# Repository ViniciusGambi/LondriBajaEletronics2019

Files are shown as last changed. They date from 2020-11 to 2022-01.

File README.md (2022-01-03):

# LondriBajaEletronics2019

> Este repositório conta um pouco a jornada da evolução do subsistema de elétrica da equipe LondriBaja entre novembro de 2018 e março de 2020. Os detalhes de implementação de cada uma das partes do projeto citadas estão sendo adicionadas em repositórios individuais, as quais seus links são citados aqui ao longo desse texto.

## Jornada

Em Agosto de 2018, novatos na equipe, que naquele momento estava sem membros no subsistema de elétrica, topamos o desafio de mesmo sem estar cursando graduação nas áreas afins, estudar o necessário para conseguir levar um sistema de segurança robusto para a competição, que não gerasse alto número de rechecks para a equipe. A competição Regional Sul seria em outubro. Trabalhamos duro aqueles dois meses para isso. Conseguimos finalizar alguns dias antes da competição, e observando as necessidades da equipe para aquele momento, projetamos um simples sistema para aferir níveis baixos de combustível, de fabricação manual, bem simples, mas que funcionava. Conseguimos chegar na competição e o resultado foi 0 rechecks, e conseguimos uma boa nota, embora marinheiros de primeira viagem. O feedback dos juízes e experiências trocadas com as demais equipes nos mostravam que o segredo era começar com pouco, mas fazer bem feito. Isso nos deu ânimo e mostrava que estávamos no caminho certo. 

Iniciamos então uma nova fase. Definimos então algumas metas. O prazo final era a competição Nacional em março de 2020. Colheríamos mais feedbacks dos juízes nas competições Nacional de 2019, em fevereiro, e Regional Sul de novembro de 2020.

- Implementar o primeiro sistema de instrumentação desenvolvido pela equipe
- Otimizar a proteção contra líquidos do então atual sistema de segurança da equipe
- Desenvolver um sensor de baixo custo para aferir o deslocamento da suspensão
- Desenvolver um aplicativo que facilitasse o processo de fazer inspeções de segurança

### A instalação elétrica

Toda a instalação elétrica do veículo foi novamente projetada em busca de reduzir a massa total do sistema, torná-la mais robusta e mais resistente a líquidos, e mais modular em busca de acelerar o processo de manutenção. O chicote foi fabricado  com tubo anti chamas, conectores IP66, prensa-cabos.Foram projetadas caixas vedadas, fabricadas com impressão 3d e borrachas para a proteção contra líquidos dos botões de emergência.

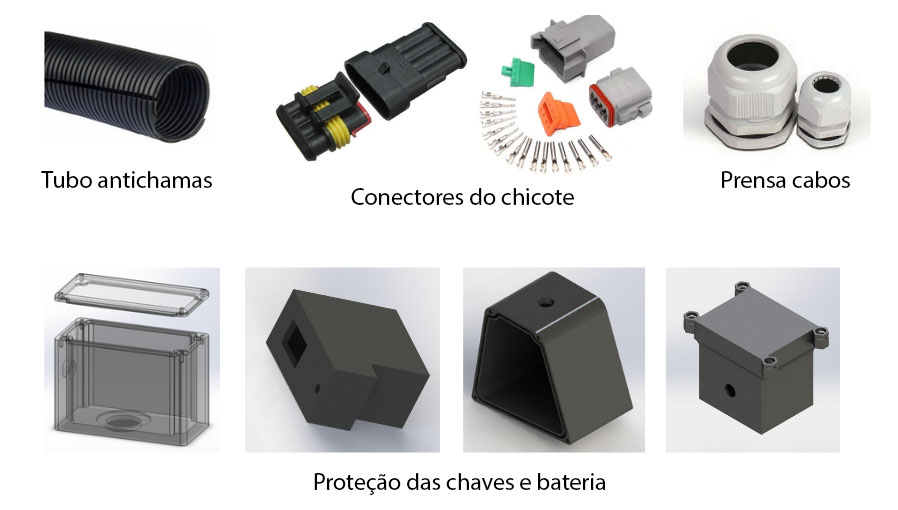
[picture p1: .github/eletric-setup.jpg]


### Sensoriamento

Seguindo o princípio de fazer algo enxuto, simples porém bem feito, para essa primeira versão foi optado por aferir 3 grandezas: RPM do motor, velocidade do veículo e nível de combustível. Os métodos escolhido para RPM foi extrair os pulsos gerados na bobina da vela, para a velocidade foi o posicionamento de um sensor indutivo no eixo da roda para contagem de pulsos, e para o combustível posicionar sensores capacitivos digitais externos ao tanque (visto que a competição proíbe utilizar sensores dentro do tanque). Mais detalhes podem ser vistos nos repositórios individuais (a serem criados).

### Projeto Elétrico e Eletrônico

O diagrama abaixo mostra como ficou organizado o sistema de segurança junto ao sistema eletrônico. 

O sistema eletrônico foi dividido em duas PCB’s, uma ECU, principal, que cuida do do controle das tensões, conecta o microcontrolador, que trabalha os dados, as entradas dos sensores, e expõe os dados para a Serial e outra PCB, que é um display com leds e displays de 7 segmentos que é utilizada como painel. 
O controle das tensões é feito por dois reguladores buck por apresentarem eficiências mais altas. O microcontrolador, um ATMega328p, foi escolhido para garantir o andamento do projeto no futuro da equipe. Como em nossa universidade não temos alunos cursando a área de eletrônica e afins, essa escolha facilita para que o projeto não fique estagnado até que futuros novos membros possam aprender a programar microcontroladores de baixo nível, pelo fato desse microcontrolador poder ser programado com a biblioteca Arduino, que tem uma grande comunidade e é de fácil aprendizagem. E mesmo assim, se adequa aos requisitos do projeto, atendendo as necessidades do projeto. Os esquemáticos e detalhes da implementação podem ser extraídos nos repositório X.

Foram projetadas caixas vedadas, como as do sistema de segurança, para o sistema de instrumentação. Foram desenvolvidas duas versões das caixas de proteção nesse tempo. A primeira foi projetada em forma de gaveta, em busca de fácil manutenção caso necessário, e guardava ambas as duas PCBs. É a implementada no veículo ao fim deste projeto. A segunda versão separa as PCB’s em duas caixas, em busca de maior modularidade, e substitui os conectores que são utilizadas na primeira versão, por sensores automotivos que se conectam diretamente a PCB, para tornar a solução mais automotiva, e retirar os prensa-cabos. Essa versão será fabricada em 2020, mas o projeto já está pronto ao fim deste ciclo. 

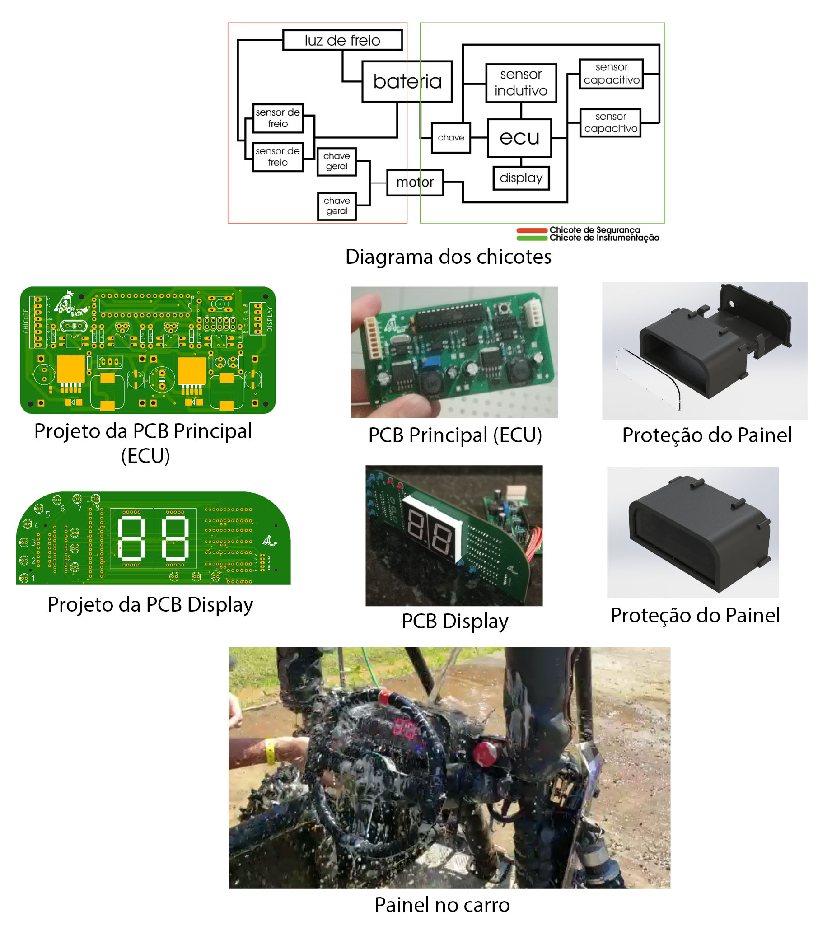
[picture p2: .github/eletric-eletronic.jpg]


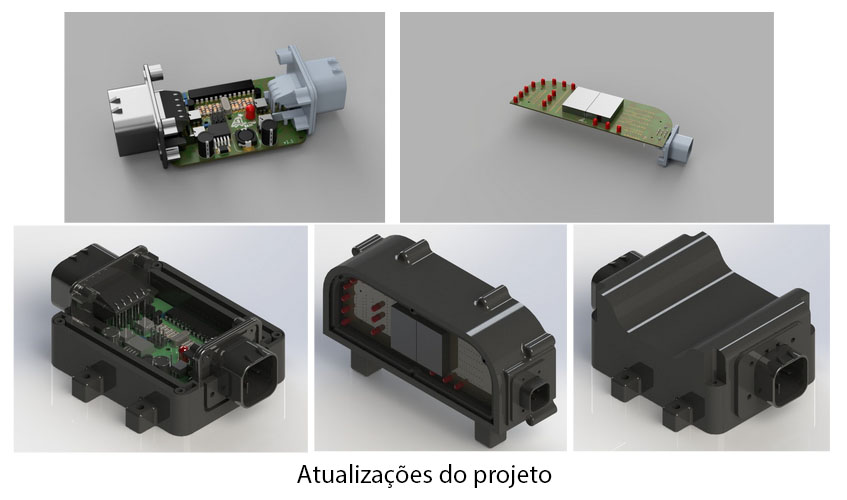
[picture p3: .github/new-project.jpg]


### User Interface e Registro de dados

Para exibir os dados aferidos pelo sistema de instrumentação, foi desenhada uma interface para a exibição dos dados. Para o registro de dados para análises, foi desenvolvido um aplicativo Android que faz registro (como um data logger) dos dados expostos na Serial. (link aqui)

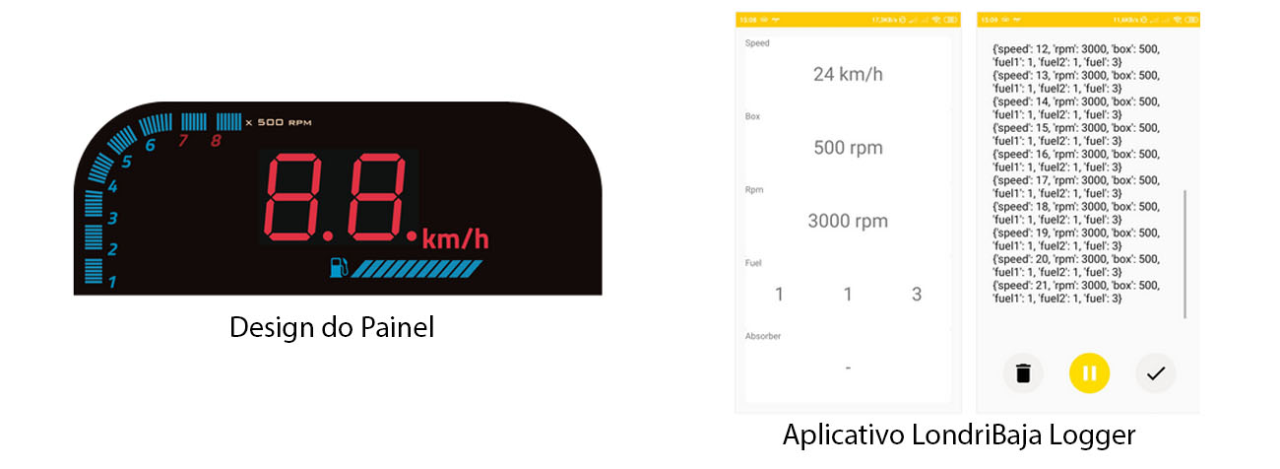
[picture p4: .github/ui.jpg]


### Validação

Todas as grandezas aferidas foram validadas e ajustadas com equipamentos com valores de referência confiáveis. A validação de RPM do motor foi feita por meio de um tacômetro óptico em bancada. Os valores de combustível foram validados em laboratório. Para a velocidade, pela falta de acesso a um equipamento calibrado de referência, desenvolvemos uma aplicação que extrai os dados de velocidade do aplicativo Waze (por ser a fonte mais segura acessível a equipe) por processamento de imagem, e os guarda registrados em função do tempo em uma planilha para a análise e comparação posterior.

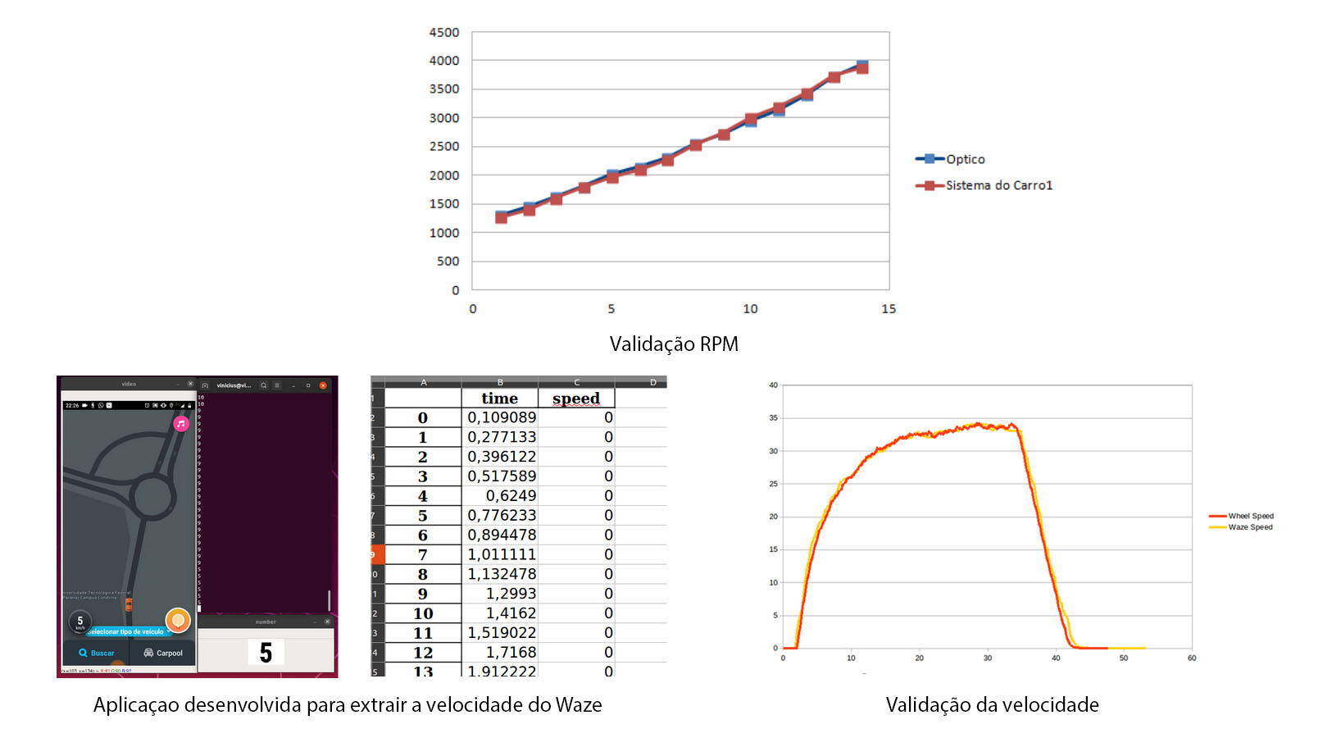
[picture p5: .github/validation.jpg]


### Extra

A partir de uma necessidade do subsistema de suspensão, que precisava de dados de deslocamento da suspensão, verificamos a possibilidade da compra de um sensor para isso. Como o valor escapava ao orçamento, buscamos uma forma de aferir essa grandeza com um sensor de baixo custo. Inicialmente realizamos alguns testes com um acelerômetro MPU6050, entretanto em virtude da baixa precisão do sensor, o acúmulo de erros ao longo do tempo tornava inviável a integral da aceleração para retirar o deslocamento. Desenvolvemos então uma solução melhor, barata, mais robusta, e com grande precisão com impressão 3D, duas barras lineares e um encoder óptico aproveitados de uma impressora velha. Esse projeto pode ser visualizado nesse outro repositório (a ser upado). 

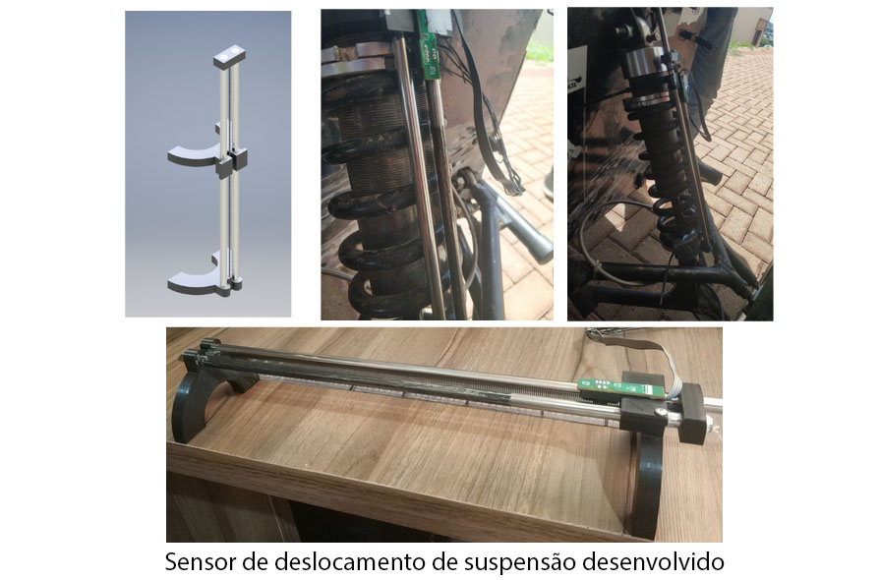
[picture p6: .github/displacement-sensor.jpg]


Outro projeto desenvolvido no ano foi um aplicativo para tornar fácil e rápido o processo da inspeção de segurança, possibilitando que a equipe os faça com mais frequência, com o objetivo de ajudar na redução dos rechecks da equipe. O link do repositório desse projeto será adicionado aqui.

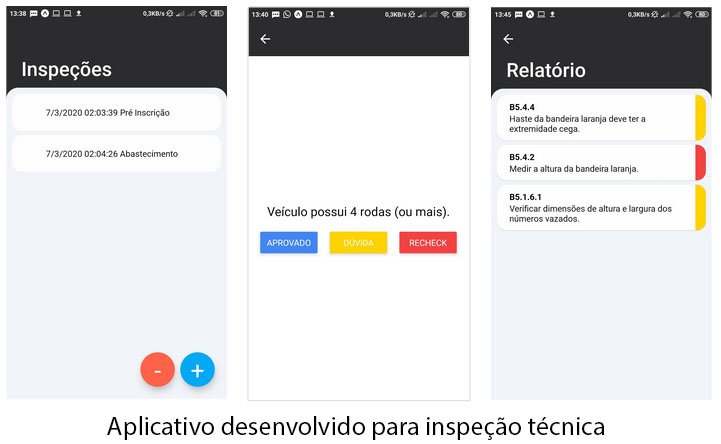
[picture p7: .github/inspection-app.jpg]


### Resultados

Com as implementações feitas, os objetivos citados anteriormente foram atingidos. Ficamos contentes por nossa evolução nesse período. Saímos de uma equipe que não tinha notas de projeto elétrico até então para o 3º melhor projeto eletrônico do Regional Sul 2019 (entre as 31 equipes inscritas) e o 13º (entre as 78 inscritas) no Nacional 2020. Deixaremos aqui também o banner da apresentação final desse projeto no Nacional de Março de 2020.

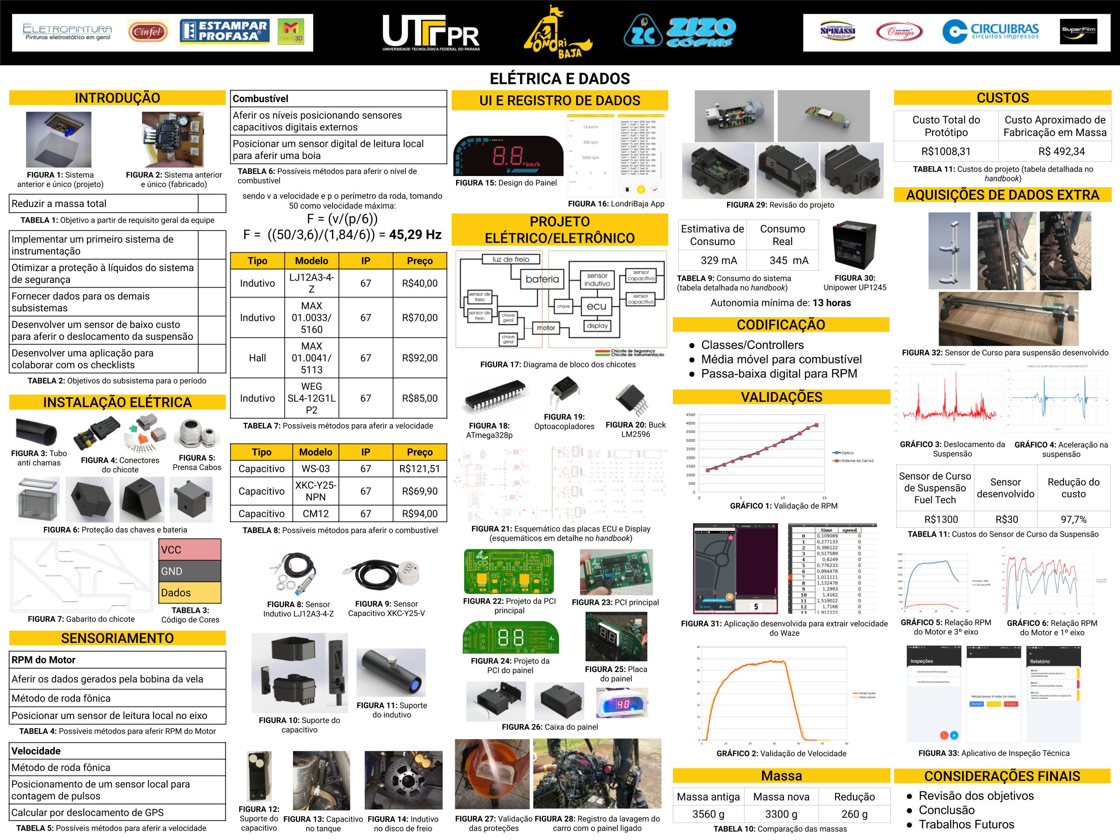
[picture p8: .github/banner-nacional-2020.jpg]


## Os autores

Cauê Gaffo, Giovani David e Vinicius Gambi abraçaram o subsistema e lideraram esse processo. No meio de 2019, tivemos a chegada dos trainees Ana Gama, Beatriz Yukari e Victor Toshio que muito ajudaram na fabricação e manutenção do projeto, e darão os próximos passos nessa evolução.

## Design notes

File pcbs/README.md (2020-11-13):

### v1

<p align="center">
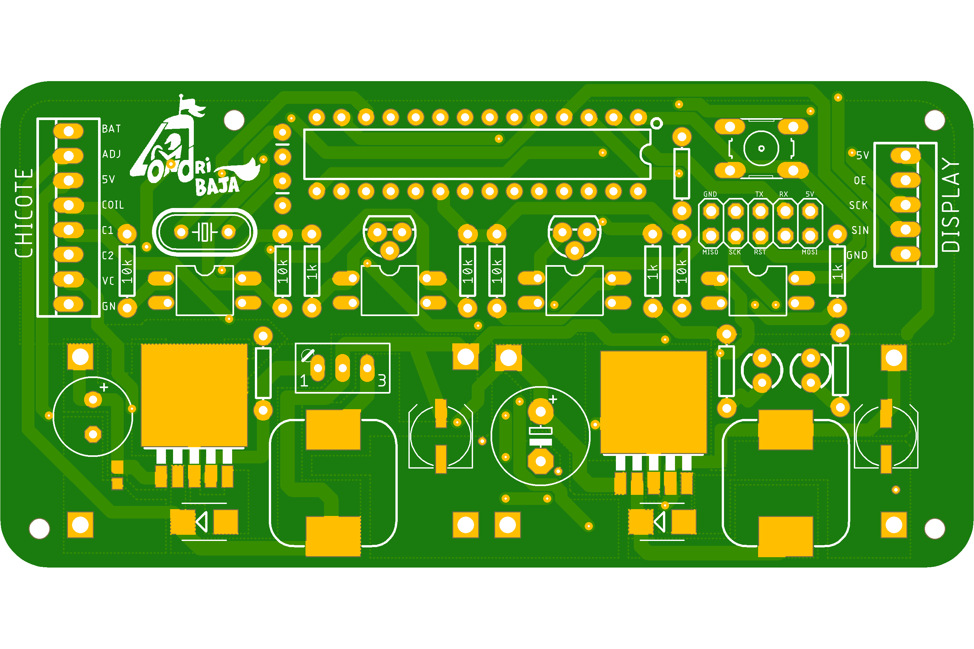
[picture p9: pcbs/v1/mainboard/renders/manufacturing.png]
    
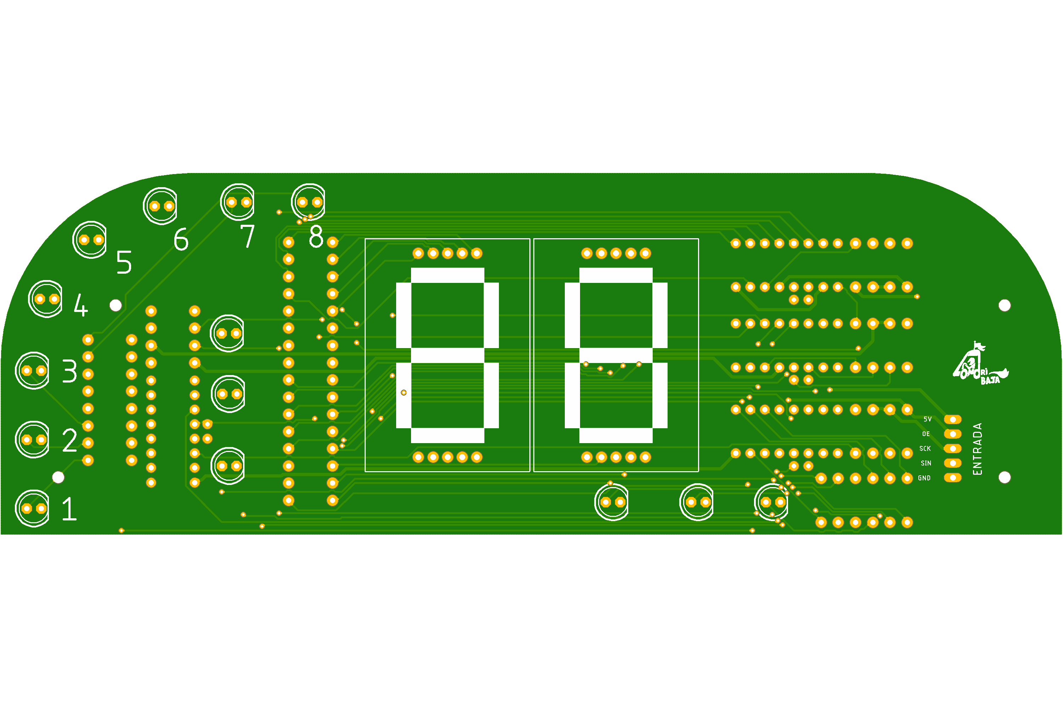
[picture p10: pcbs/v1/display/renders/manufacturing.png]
    
</p>

### v2

<p align="center">
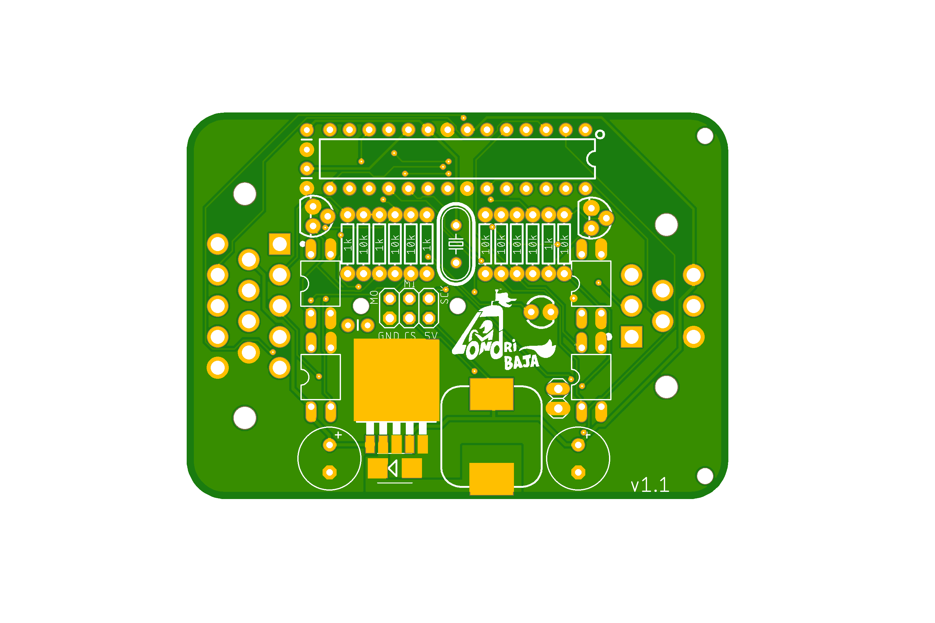
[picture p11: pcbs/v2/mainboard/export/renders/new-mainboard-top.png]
    
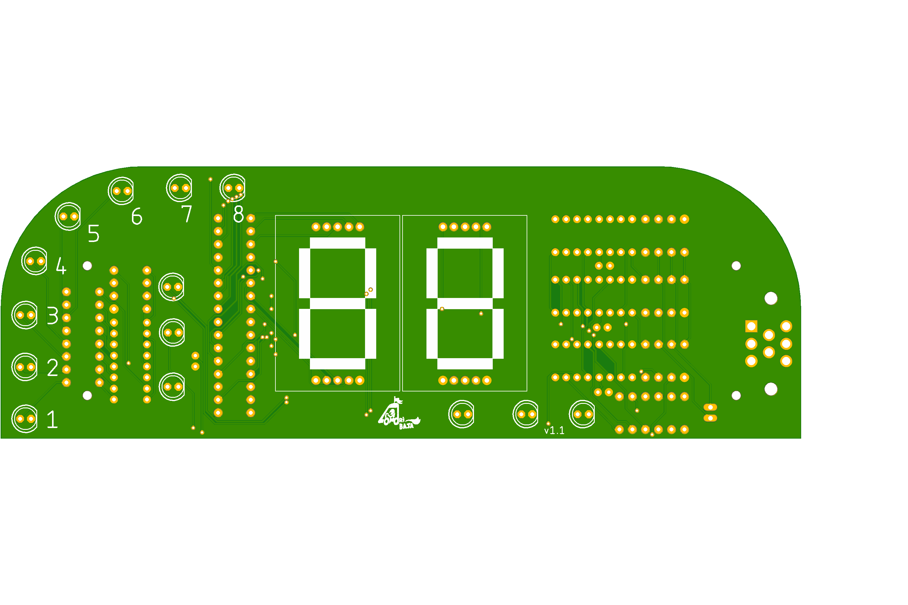
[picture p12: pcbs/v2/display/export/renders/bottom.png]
    
</p>

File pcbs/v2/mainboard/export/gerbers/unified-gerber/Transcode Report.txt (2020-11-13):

   ---- Transcoding 'C:\Users\Workstation\Documents\Baja 2020\pcbs\out\unified-gerber\combined.gbs' ----   Wed Feb 19 16:48:30 2020

D10   --> D100
D11   --> D101
D12   --> D102
D13   --> D103
D14   --> D104
D15   --> D105
D16   --> D106
D17   --> D107
D18   --> D108
D19   --> D109
D20   --> D110
D21   --> D111
D22   --> D112
D23   --> D113
D24   --> D114
D36   --> D115
D37   --> D116
D38   --> D117
D39   --> D118
D40   --> D119
D41   --> D120
D42   --> D121
D43   --> D122
D44   --> D123
-----------------------------------------------------------------

   ---- Transcoding 'C:\Users\Workstation\Documents\Baja 2020\pcbs\out\unified-gerber\combined.GKO' ----   Wed Feb 19 16:48:30 2020

D10   --> D124
-----------------------------------------------------------------

   ---- Transcoding 'C:\Users\Workstation\Documents\Baja 2020\pcbs\out\unified-gerber\combined.gml' ----   Wed Feb 19 16:48:30 2020

D10   --> D125
D11   --> D126
D22   --> D127
D23   --> D128
-----------------------------------------------------------------

   ---- Transcoding 'C:\Users\Workstation\Documents\Baja 2020\pcbs\out\unified-gerber\combined.gtl' ----   Wed Feb 19 16:48:30 2020

D15   --> D129
D16   --> D130
D17   --> D131
D18   --> D132
D19   --> D133
D20   --> D134
D21   --> D135
D22   --> D136
D23   --> D137
D24   --> D138
D25   --> D139
D42   --> D140
D43   --> D141
D44   --> D142
-----------------------------------------------------------------

   ---- Transcoding 'C:\Users\Workstation\Documents\Baja 2020\pcbs\out\unified-gerber\combined.gtp' ----   Wed Feb 19 16:48:32 2020

D10   --> D143
D11   --> D144
D12   --> D145
D13   --> D146
-----------------------------------------------------------------

   ---- Transcoding 'C:\Users\Workstation\Documents\Baja 2020\pcbs\out\unified-gerber\combined.gts' ----   Wed Feb 19 16:48:32 2020

D10   --> D147
D11   --> D148
D12   --> D149
D13   --> D150
D14   --> D151
D15   --> D152
D16   --> D153
D17   --> D154
D18   --> D155
D19   --> D156
D20   --> D157
D21   --> D158
D22   --> D159
D23   --> D160
D24   --> D161
D25   --> D162
D26   --> D163
D27   --> D164
D28   --> D165
D39   --> D166
D40   --> D167
D41   --> D168
D42   --> D169
D43   --> D170
D44   --> D171
D45   --> D172
D46   --> D173
D47   --> D174
D48   --> D175
-----------------------------------------------------------------

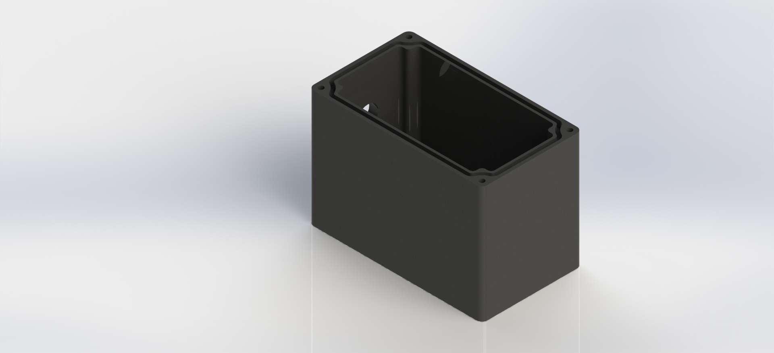
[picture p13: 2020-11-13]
mechanical/v2/renders/caixa-botao-piloto.JPG

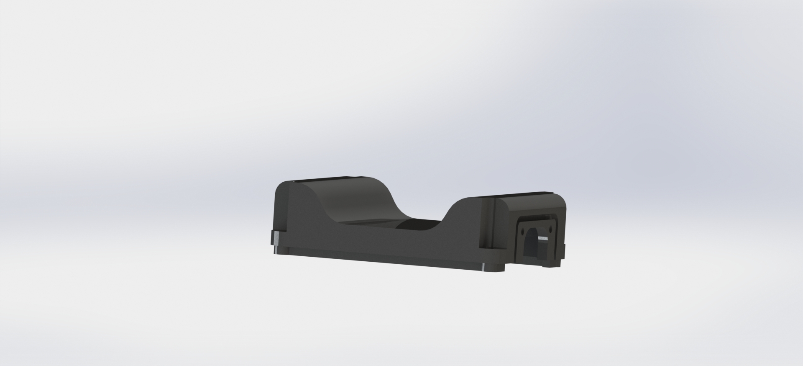
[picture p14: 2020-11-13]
mechanical/v2/renders/tampa-mainboard-3.JPG

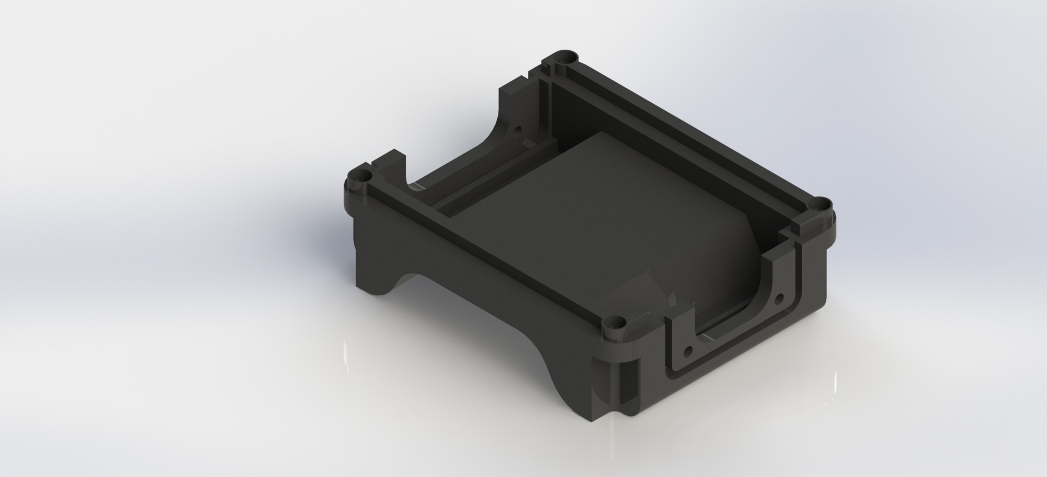
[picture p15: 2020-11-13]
mechanical/v2/renders/tampa-mainboard-1.JPG

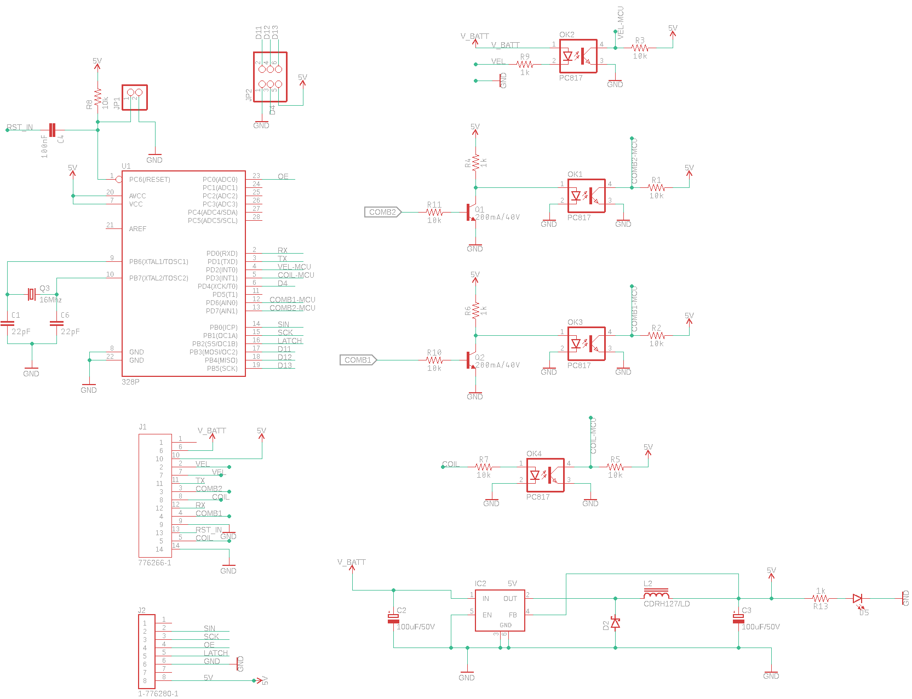
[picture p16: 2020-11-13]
pcbs/v2/mainboard/export/renders/schematic.png

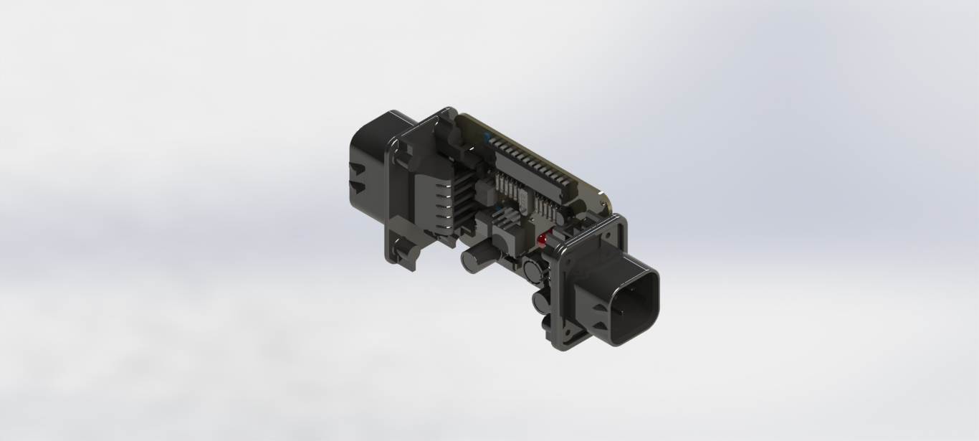
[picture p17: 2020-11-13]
mechanical/v2/renders/mainboard.JPG

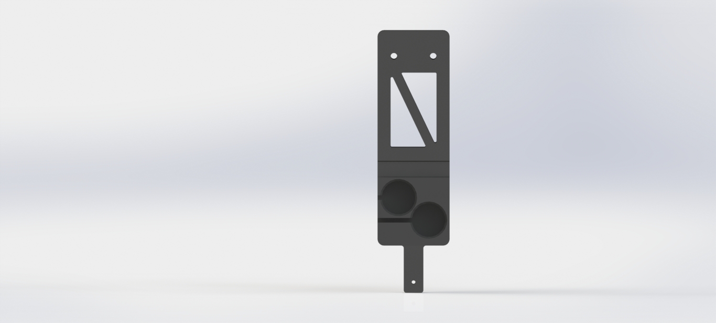
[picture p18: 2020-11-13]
mechanical/v2/renders/suporte-sensor-combustivel-2.JPG

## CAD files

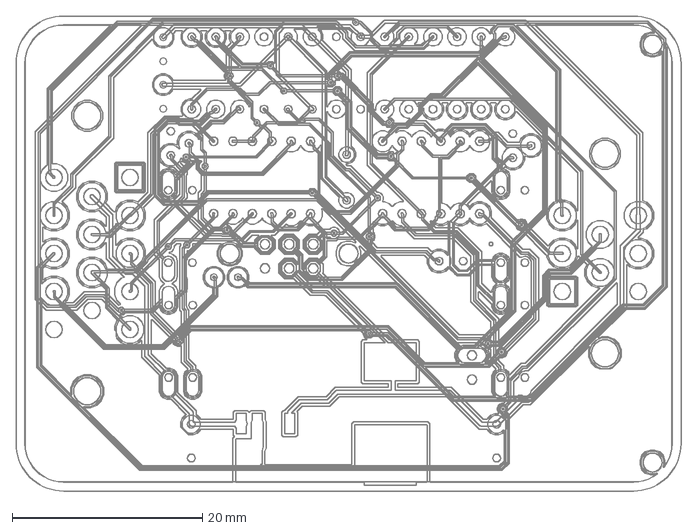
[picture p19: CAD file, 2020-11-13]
pcbs/v2/mainboard/export/dxf/new-mainboard.dxf
70.0 x 50.0 mm

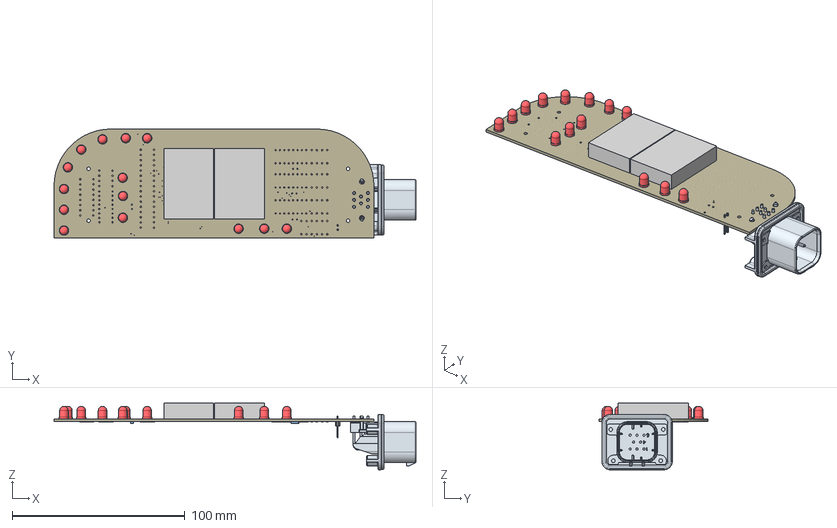
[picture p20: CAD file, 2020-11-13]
pcbs/v2/display/export/step/new-display.step
209.3 x 63.0 x 38.6 mm
Board
LED5MM x 14
DISPLAY1.2 x 2
SN74HC595N x 4
0.1uF x 4
1X02

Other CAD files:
pcbs/v2/display/export/dxf/new-display.dxf

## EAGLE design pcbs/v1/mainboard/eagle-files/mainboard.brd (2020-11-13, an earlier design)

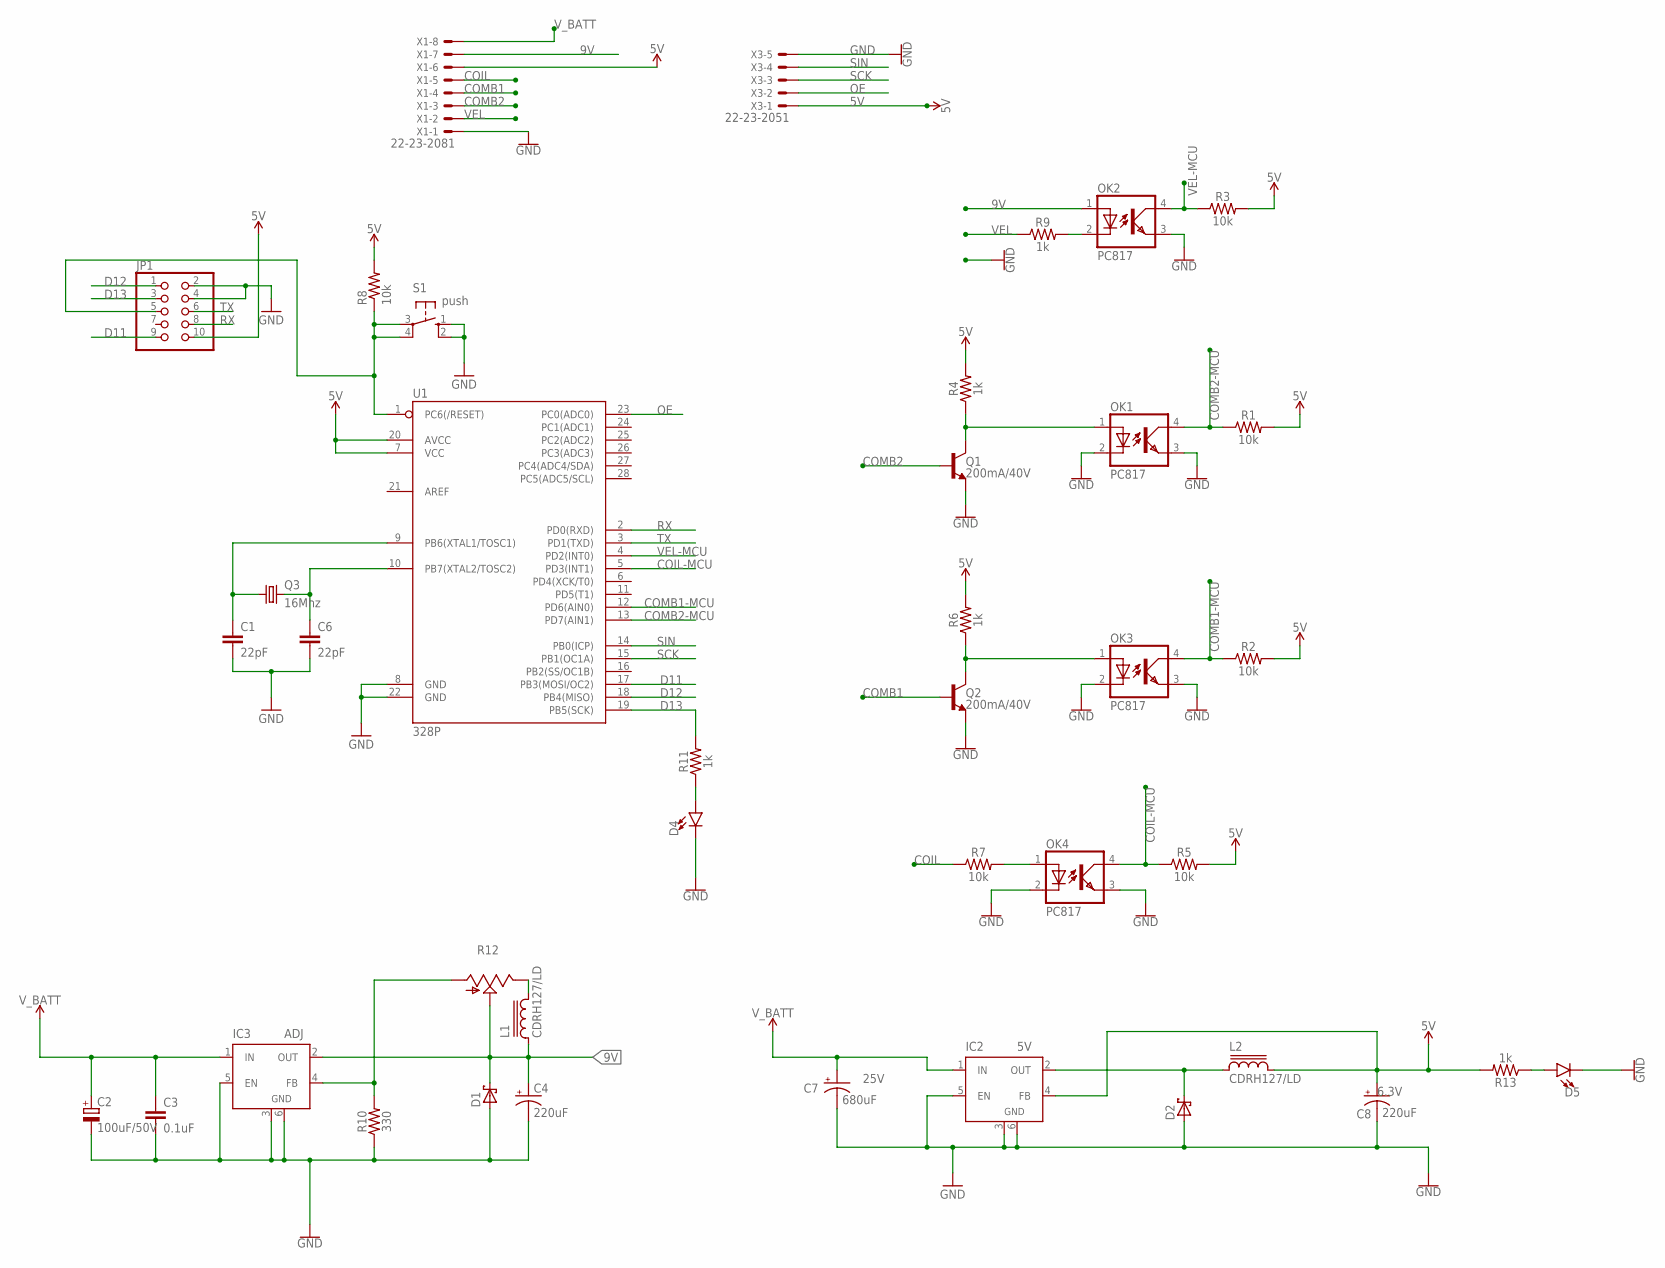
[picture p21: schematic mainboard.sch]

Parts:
C1, C6: 22pF; CAP-PTH-2.54
C2: 100uF/50V; E3,5-8
C3: 0.1uF; 0603
C4: 220uF; UD-6,3X5,8_NICHICON
C7: 680uF; E5-10,5; VOLTAGE 25V
C8: 220uF; UD-6,3X5,8_NICHICON; VOLTAGE 6.3V
D1, D2: SCHOTTKY-DIODESMD; SMB
D4, D5: LED3MM; LED_3MM
IC2: 5V; TO263-5
IC3: ADJ; TO263-5
JP1: PINHD-2X5; 2X05
L1, L2: CDRH127/LD
OK1, OK2, OK3, OK4: PC817; DIL04
Q1, Q2: 200mA/40V; TO-92
Q3: 16Mhz; HC49U-V
R1, R2, R3, R5, R7, R8: 10k; AXIAL-0.3
R4, R6, R9, R11, R13: 1k; AXIAL-0.3
R10: 330; AXIAL-0.3
R12: TRIM_US-S64W; S64W
S1: push; B3F-10XX
U1: 328P; DIP28
X1: 22-23-2081
X3: 22-23-2051

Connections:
5V: C8.+, IC2.4 (FB), JP1.10, L2.2, R1.P$2 (2), R2.P$2 (2), R3.P$2 (2), R4.P$2 (2), R5.P$2 (2), R6.P$2 (2), R8.P$2 (2), R13.P$2 (2), U1.7 (VCC), U1.20 (AVCC), X1.6, X3.1
9V: C4.+, D1.C, IC3.2 (OUT), L1.1, OK2.1 (A), R12.S, X1.7
COIL: R7.P$1 (1), X1.5
COIL-MCU: OK4.4 (COL), R5.P$1 (1), U1.5 (PD3(INT1))
COMB1: Q2.2 (B), X1.4
COMB1-MCU: OK3.4 (COL), R2.P$1 (1), U1.12 (PD6(AIN0))
COMB2: Q1.2 (B), X1.3
COMB2-MCU: OK1.4 (COL), R1.P$1 (1), U1.13 (PD7(AIN1))
D11: JP1.9, U1.17 (PB3(MOSI/OC2))
D12: JP1.1, U1.18 (PB4(MISO))
D13: JP1.3, R11.P$2 (2), U1.19 (PB5(SCK))
GND: C1.2, C2.-, C3.2, C4.-, C6.2, C7.-, C8.-, D1.A, D2.A, D4.K (C), D5.K (C), IC2.3 (GND), IC2.5 (EN), IC2.6 (GND), IC3.3 (GND), IC3.5 (EN), IC3.6 (GND), JP1.2, JP1.4, OK1.2 (C), OK1.3 (EMIT), OK2.3 (EMIT), OK3.2 (C), OK3.3 (EMIT), OK4.2 (C), OK4.3 (EMIT), Q1.1 (E), Q2.1 (E), R10.P$1 (1), S1.1 (S), S1.2 (S1), U1.8 (GND), U1.22 (GND), X1.1, X3.5
unnamed: OK4.1 (A), R7.P$2 (2)
unnamed: OK2.2 (C), R9.P$2 (2)
unnamed: OK1.1 (A), Q1.3 (C), R4.P$1 (1)
unnamed: OK3.1 (A), Q2.3 (C), R6.P$1 (1)
unnamed: C1.1, Q3.1, U1.9 (PB6(XTAL1/TOSC1))
unnamed: C6.1, Q3.2, U1.10 (PB7(XTAL2/TOSC2))
unnamed: JP1.5, R8.P$1 (1), S1.3, S1.4 (P1), U1.1 (PC6(/RESET))
unnamed: D5.A, R13.P$1 (1)
unnamed: L1.2, R12.E
unnamed: IC3.4 (FB), R10.P$2 (2), R12.A
unnamed: D4.A, R11.P$1 (1)
OE: U1.23 (PC0(ADC0)), X3.2
OUT: D2.C, IC2.2 (OUT), L2.1
RX: JP1.8, U1.2 (PD0(RXD))
SCK: U1.15 (PB1(OC1A)), X3.3
SIN: U1.14 (PB0(ICP)), X3.4
TX: JP1.6, U1.3 (PD1(TXD))
VEL: R9.P$1 (1), X1.2
VEL-MCU: OK2.4 (COL), R3.P$1 (1), U1.4 (PD2(INT0))
V_BATT: C2.+, C3.1, C7.+, IC2.1 (IN), IC3.1 (IN), X1.8

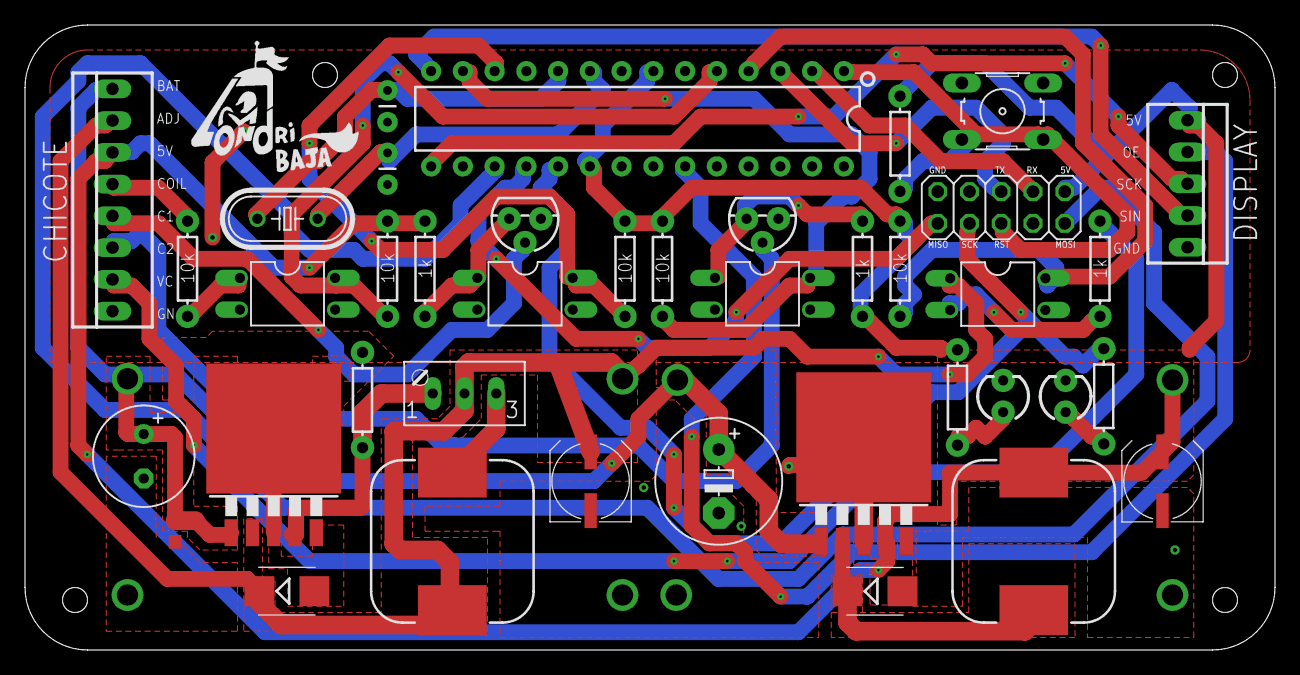
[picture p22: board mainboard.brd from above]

Board: 2 copper layers, 100.0 x 50.0 mm, 40 parts (0 on the bottom side), 32 nets.

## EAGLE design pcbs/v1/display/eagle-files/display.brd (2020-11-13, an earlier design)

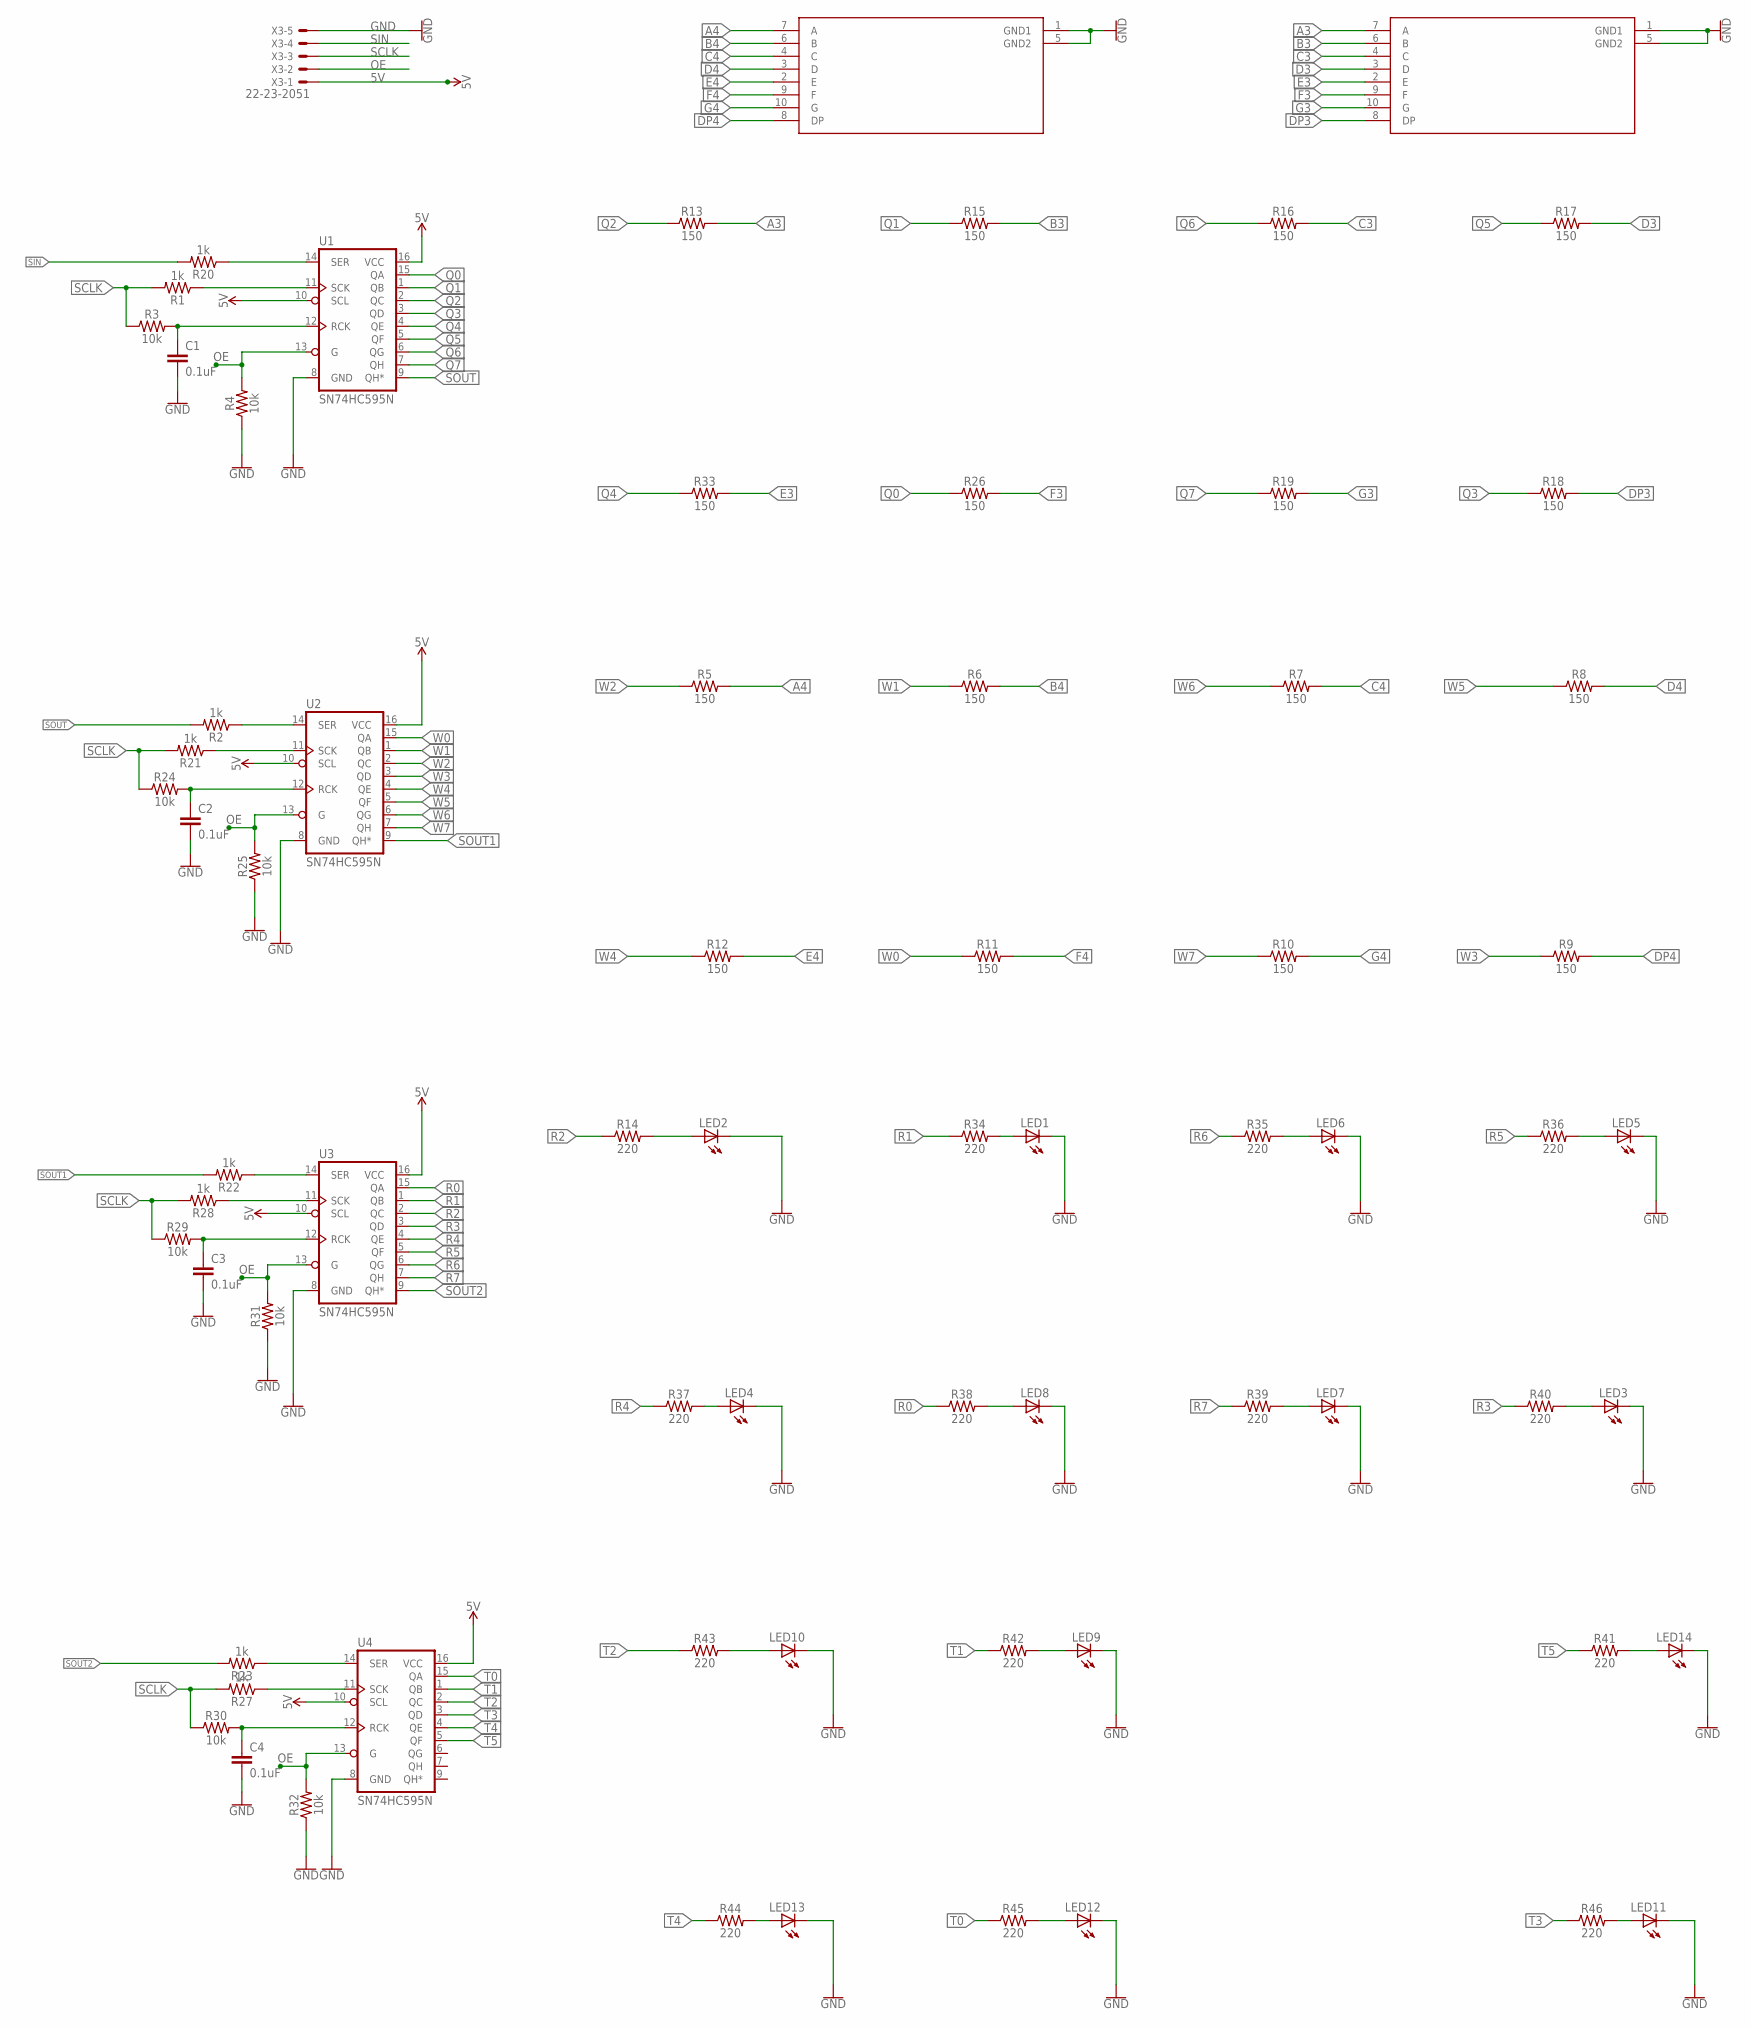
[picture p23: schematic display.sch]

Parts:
C1, C2, C3, C4: 0.1uF; CAP-PTH-2.54
LED1, LED2, LED3, LED4, LED5, LED6, LED7, LED8, LED9, LED10, LED11, LED12, LED13, LED14: LED5MM
R1, R2, R20, R21, R22, R23, R27, R28: 1k; AXIAL-0.3
R3, R4, R24, R25, R29, R30, R31, R32: 10k; AXIAL-0.3
R5, R6, R7, R8, R9, R10, R11, R12, R13, R15, R16, R17, R18, R19, R26, R33: 150; AXIAL-0.3
R14, R34, R35, R36, R37, R38, R39, R40, R41, R42, R43, R44, R45, R46: 220; AXIAL-0.3
U1, U2, U3, U4: SN74HC595N; DIP16
U$1, U$2: DISPLAY1.2; 1.2INCH
X3: 22-23-2051

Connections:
5V: U1.10 (SCL), U1.16 (VCC), U2.10 (SCL), U2.16 (VCC), U3.10 (SCL), U3.16 (VCC), U4.10 (SCL), U4.16 (VCC), X3.1
A3: R13.P$2 (2), U$1.7 (A)
A4: R5.P$2 (2), U$2.7 (A)
B3: R15.P$2 (2), U$1.6 (B)
B4: R6.P$2 (2), U$2.6 (B)
C3: R16.P$2 (2), U$1.4 (C)
C4: R7.P$2 (2), U$2.4 (C)
D3: R17.P$2 (2), U$1.3 (D)
D4: R8.P$2 (2), U$2.3 (D)
DP3: R18.P$2 (2), U$1.8 (DP)
DP4: R9.P$2 (2), U$2.8 (DP)
E3: R33.P$2 (2), U$1.2 (E)
E4: R12.P$2 (2), U$2.2 (E)
F3: R26.P$2 (2), U$1.9 (F)
F4: R11.P$2 (2), U$2.9 (F)
G3: R19.P$2 (2), U$1.10 (G)
G4: R10.P$2 (2), U$2.10 (G)
GND: C1.2, C2.2, C3.2, C4.2, LED1.K (C), LED2.K (C), LED3.K (C), LED4.K (C), LED5.K (C), LED6.K (C), LED7.K (C), LED8.K (C), LED9.K (C), LED10.K (C), LED11.K (C), LED12.K (C), LED13.K (C), LED14.K (C), R4.P$1 (1), R25.P$1 (1), R31.P$1 (1), R32.P$1 (1), U1.8 (GND), U2.8 (GND), U3.8 (GND), U4.8 (GND), U$1.1 (GND1), U$1.5 (GND2), U$2.1 (GND1), U$2.5 (GND2), X3.5
unnamed: R20.P$1 (1), U1.14 (SER)
unnamed: R1.P$1 (1), U1.11 (SCK)
unnamed: C1.1, R3.P$2 (2), U1.12 (RCK)
unnamed: R2.P$1 (1), U2.14 (SER)
unnamed: R21.P$1 (1), U2.11 (SCK)
unnamed: C2.1, R24.P$2 (2), U2.12 (RCK)
unnamed: LED4.A, R37.P$2 (2)
unnamed: LED8.A, R38.P$2 (2)
unnamed: LED7.A, R39.P$2 (2)
unnamed: LED3.A, R40.P$2 (2)
unnamed: LED5.A, R36.P$2 (2)
unnamed: LED6.A, R35.P$2 (2)
unnamed: LED1.A, R34.P$2 (2)
unnamed: LED2.A, R14.P$2 (2)
unnamed: LED10.A, R43.P$2 (2)
unnamed: R22.P$1 (1), U3.14 (SER)
unnamed: R28.P$1 (1), U3.11 (SCK)
unnamed: C3.1, R29.P$2 (2), U3.12 (RCK)
unnamed: LED9.A, R42.P$2 (2)
unnamed: LED11.A, R46.P$2 (2)
unnamed: LED14.A, R41.P$2 (2)
unnamed: LED12.A, R45.P$2 (2)
unnamed: R23.P$1 (1), U4.14 (SER)
unnamed: R27.P$1 (1), U4.11 (SCK)
unnamed: C4.1, R30.P$2 (2), U4.12 (RCK)
unnamed: LED13.A, R44.P$2 (2)
OE: R4.P$2 (2), R25.P$2 (2), R31.P$2 (2), R32.P$2 (2), U1.13 (G), U2.13 (G), U3.13 (G), U4.13 (G), X3.2
Q0: R26.P$1 (1), U1.15 (QA)
Q1: R15.P$1 (1), U1.1 (QB)
Q2: R13.P$1 (1), U1.2 (QC)
Q3: R18.P$1 (1), U1.3 (QD)
Q4: R33.P$1 (1), U1.4 (QE)
Q5: R17.P$1 (1), U1.5 (QF)
Q6: R16.P$1 (1), U1.6 (QG)
Q7: R19.P$1 (1), U1.7 (QH)
R0: R38.P$1 (1), U3.15 (QA)
R1: R34.P$1 (1), U3.1 (QB)
R2: R14.P$1 (1), U3.2 (QC)
R3: R40.P$1 (1), U3.3 (QD)
R4: R37.P$1 (1), U3.4 (QE)
R5: R36.P$1 (1), U3.5 (QF)
R6: R35.P$1 (1), U3.6 (QG)
R7: R39.P$1 (1), U3.7 (QH)
SCLK: R1.P$2 (2), R3.P$1 (1), R21.P$2 (2), R24.P$1 (1), R27.P$2 (2), R28.P$2 (2), R29.P$1 (1), R30.P$1 (1), X3.3
SIN: R20.P$2 (2), X3.4
SOUT: R2.P$2 (2), U1.9 (QH*)
SOUT1: R22.P$2 (2), U2.9 (QH*)
SOUT2: R23.P$2 (2), U3.9 (QH*)
T0: R45.P$1 (1), U4.15 (QA)
T1: R42.P$1 (1), U4.1 (QB)
T2: R43.P$1 (1), U4.2 (QC)
T3: R46.P$1 (1), U4.3 (QD)
T4: R44.P$1 (1), U4.4 (QE)
T5: R41.P$1 (1), U4.5 (QF)
W0: R11.P$1 (1), U2.15 (QA)
W1: R6.P$1 (1), U2.1 (QB)
W2: R5.P$1 (1), U2.2 (QC)
W3: R9.P$1 (1), U2.3 (QD)
W4: R12.P$1 (1), U2.4 (QE)
W5: R8.P$1 (1), U2.5 (QF)
W6: R7.P$1 (1), U2.6 (QG)
W7: R10.P$1 (1), U2.7 (QH)

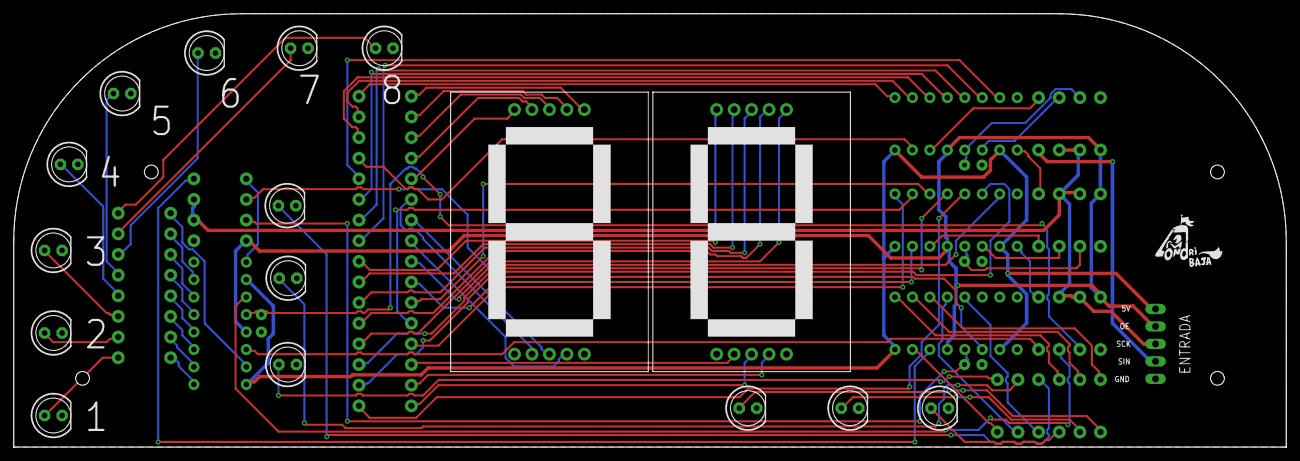
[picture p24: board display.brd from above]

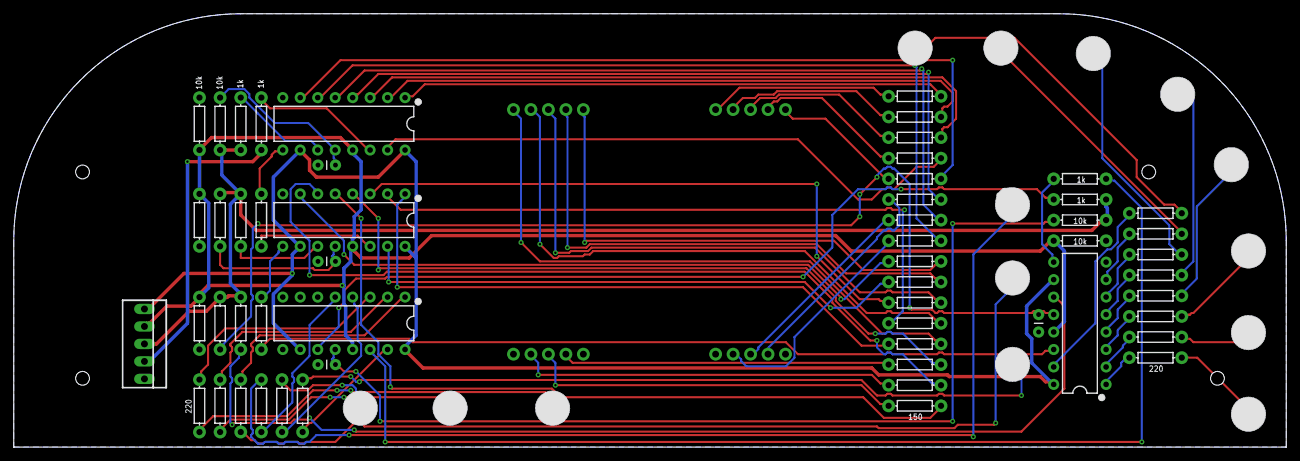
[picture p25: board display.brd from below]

Board: 2 copper layers, 185.0 x 63.0 mm, 71 parts (55 on the bottom side), 80 nets.

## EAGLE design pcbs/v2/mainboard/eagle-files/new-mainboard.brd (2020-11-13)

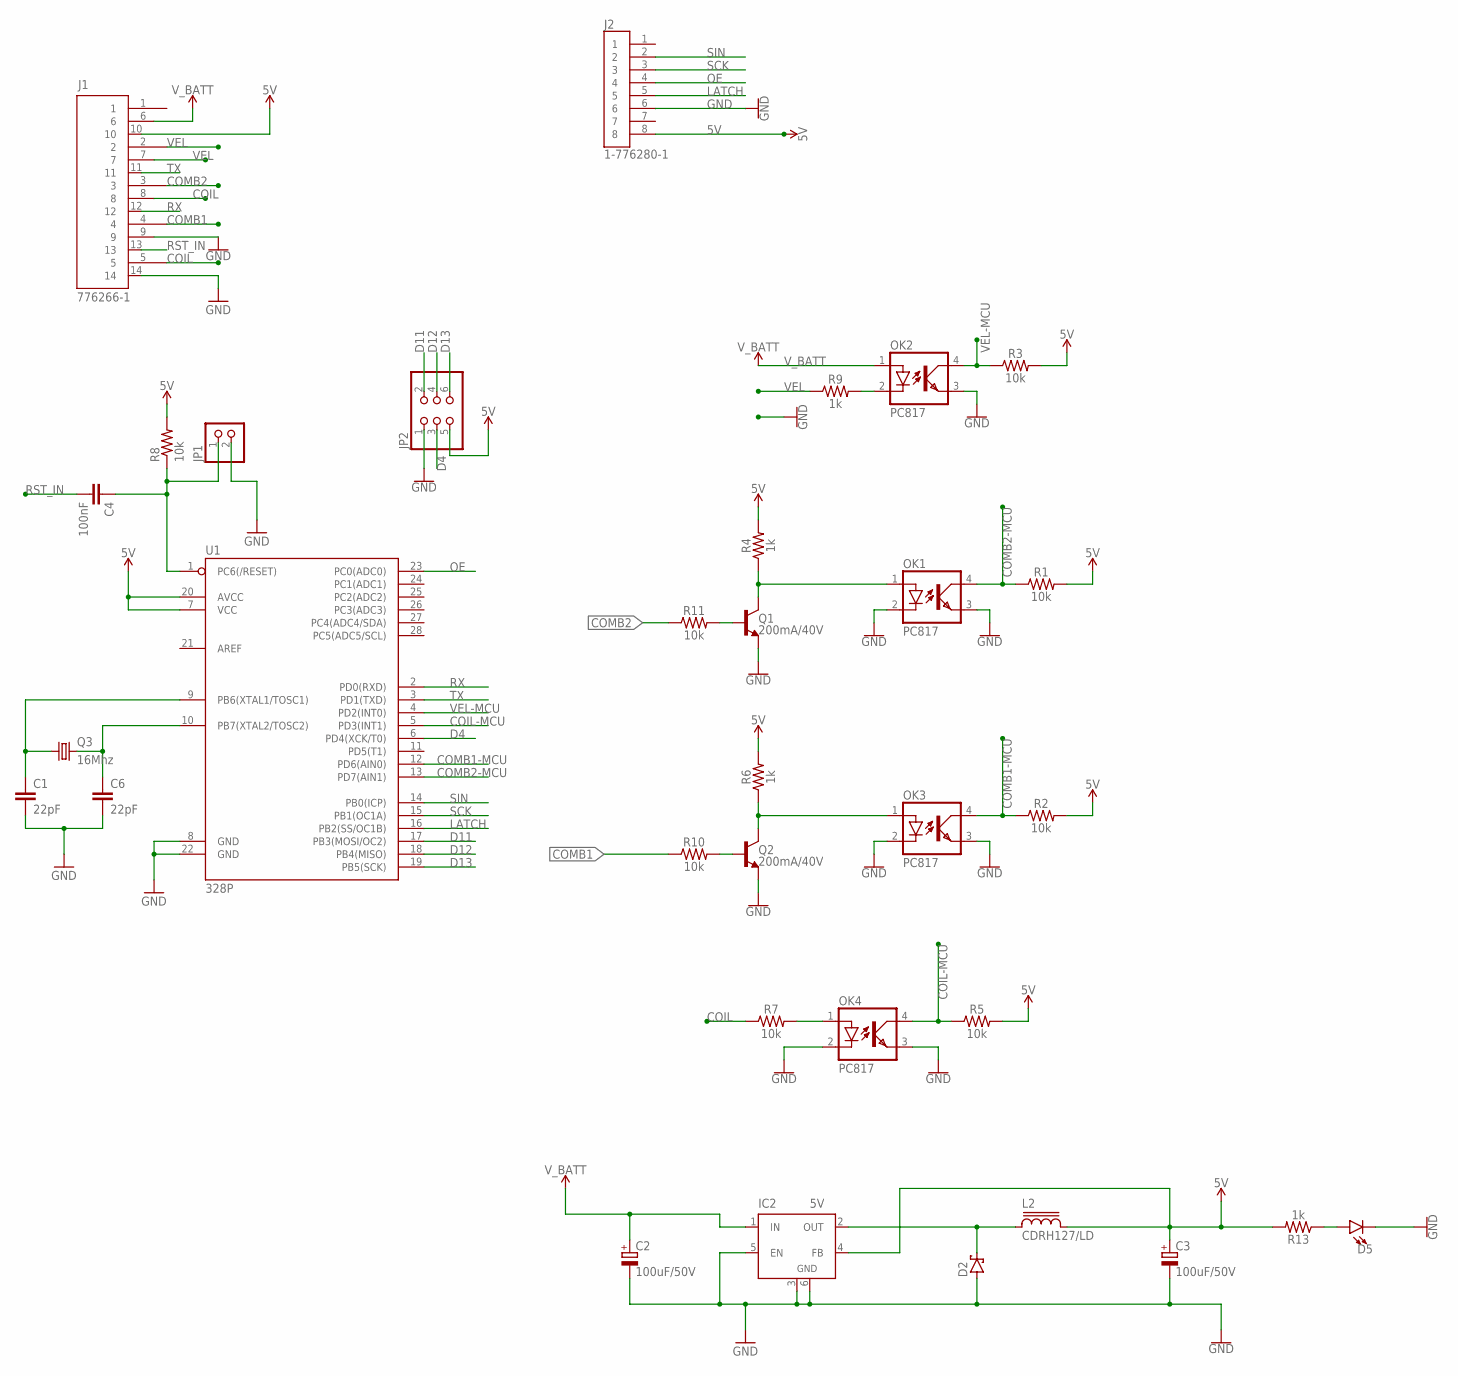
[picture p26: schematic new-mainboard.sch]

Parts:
C1, C6: 22pF; CAP-PTH-2.54
C2, C3: 100uF/50V; E3,5-8
C4: 100nF; CAP-PTH-2.54
D2: SCHOTTKY-DIODESMD; SMB
D5: LED3MM; LED_3MM
IC2: 5V; TO263-5
J1: 776266-1; TE_776266-1
J2: 1-776280-1; TE_1-776280-1
JP1: PINHD-1X2; 1X02
JP2: PINHD-2X3; 2X03
L2: CDRH127/LD
OK1, OK2, OK3, OK4: PC817; DIL04
Q1, Q2: 200mA/40V; TO-92
Q3: 16Mhz; HC49U-V
R1, R2, R3, R5, R7, R8, R10, R11: 10k; AXIAL-0.3
R4, R6, R9, R13: 1k; AXIAL-0.3
U1: 328P; DIP28

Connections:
5V: C3.+, IC2.4 (FB), J1.10, J2.8, JP2.5, L2.2, R1.P$2 (2), R2.P$2 (2), R3.P$2 (2), R4.P$2 (2), R5.P$2 (2), R6.P$2 (2), R8.P$2 (2), R13.P$2 (2), U1.7 (VCC), U1.20 (AVCC)
COIL: J1.5, J1.8, R7.P$1 (1)
COIL-MCU: OK4.4 (COL), R5.P$1 (1), U1.5 (PD3(INT1))
COMB1: J1.4, R10.P$1 (1)
COMB1-MCU: OK3.4 (COL), R2.P$1 (1), U1.12 (PD6(AIN0))
COMB2: J1.3, R11.P$1 (1)
COMB2-MCU: OK1.4 (COL), R1.P$1 (1), U1.13 (PD7(AIN1))
D4: JP2.3, U1.6 (PD4(XCK/T0))
D11: JP2.2, U1.17 (PB3(MOSI/OC2))
D12: JP2.4, U1.18 (PB4(MISO))
D13: JP2.6, U1.19 (PB5(SCK))
GND: C1.2, C2.-, C3.-, C6.2, D2.A, D5.K (C), IC2.3 (GND), IC2.5 (EN), IC2.6 (GND), J1.9, J1.14, J2.6, JP1.2, JP2.1, OK1.2 (C), OK1.3 (EMIT), OK2.3 (EMIT), OK3.2 (C), OK3.3 (EMIT), OK4.2 (C), OK4.3 (EMIT), Q1.1 (E), Q2.1 (E), U1.8 (GND), U1.22 (GND)
LATCH: J2.5, U1.16 (PB2(SS/OC1B))
unnamed: OK4.1 (A), R7.P$2 (2)
unnamed: OK2.2 (C), R9.P$2 (2)
unnamed: OK1.1 (A), Q1.3 (C), R4.P$1 (1)
unnamed: OK3.1 (A), Q2.3 (C), R6.P$1 (1)
unnamed: C1.1, Q3.1, U1.9 (PB6(XTAL1/TOSC1))
unnamed: C6.1, Q3.2, U1.10 (PB7(XTAL2/TOSC2))
unnamed: Q2.2 (B), R10.P$2 (2)
unnamed: D5.A, R13.P$1 (1)
unnamed: Q1.2 (B), R11.P$2 (2)
OE: J2.4, U1.23 (PC0(ADC0))
OUT: D2.C, IC2.2 (OUT), L2.1
RST: C4.1, JP1.1, R8.P$1 (1), U1.1 (PC6(/RESET))
RST_IN: C4.2, J1.13
RX: J1.12, U1.2 (PD0(RXD))
SCK: J2.3, U1.15 (PB1(OC1A))
SIN: J2.2, U1.14 (PB0(ICP))
TX: J1.11, U1.3 (PD1(TXD))
VEL: J1.2, J1.7, R9.P$1 (1)
VEL-MCU: OK2.4 (COL), R3.P$1 (1), U1.4 (PD2(INT0))
V_BATT: C2.+, IC2.1 (IN), J1.6, OK2.1 (A)

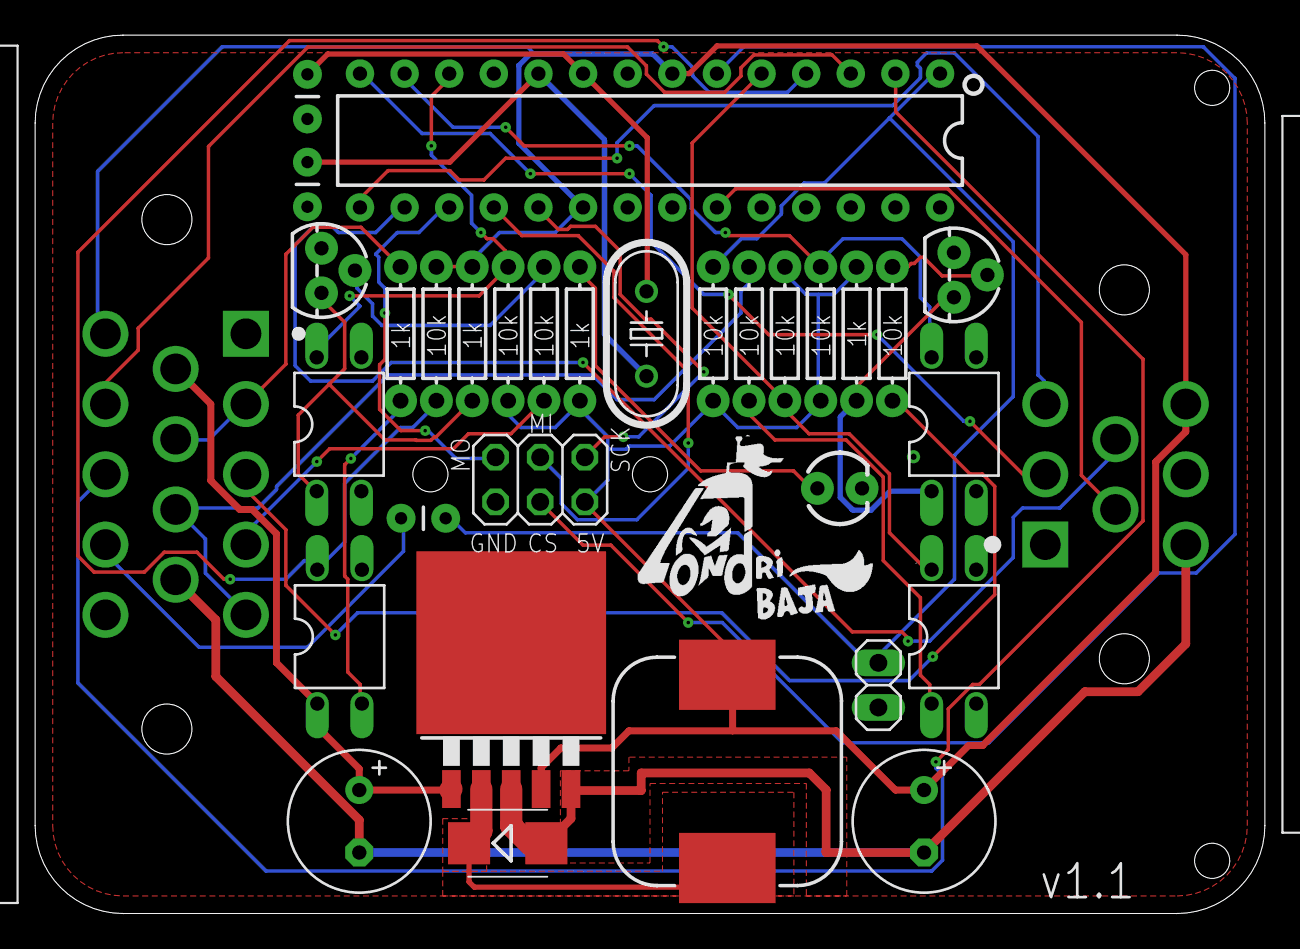
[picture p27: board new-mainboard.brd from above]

Board: 2 copper layers, 70.0 x 50.0 mm, 33 parts (0 on the bottom side), 33 nets.

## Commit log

2020-11-13 some files added
    [combined.GKO, combined.gbl, combined.gbo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]
2020-11-13 pcbs readme
2020-11-13 eagle-files folder added
    [display.brd, display.sch, mainboard.brd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]

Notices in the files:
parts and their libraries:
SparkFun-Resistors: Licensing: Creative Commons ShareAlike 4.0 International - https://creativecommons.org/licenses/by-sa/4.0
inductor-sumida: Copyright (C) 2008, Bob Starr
